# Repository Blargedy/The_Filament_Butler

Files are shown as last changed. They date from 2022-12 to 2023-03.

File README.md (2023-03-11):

# The Filament Butler
In short, this is a manually-operated drop-in replacement for the Prusa MMU2, for use in high(ish) temperature printing. 



I put my two Prusa Mk3s into enclosures in order to print ABS/ASA without warping. Unfortunately, the control boards of each MMU couldn't handle the elevated temperatures (~50C) and burned out. Instead of moving the electronics of the MMU2 out of the hot chamber, I decided to completely eliminate the automated swapping of filament.  I run the [Tefnut](https://github.com/Blargedy/Tefnut_Filament_Handling) system and wanted to maintain compatibility with it. The Filament Butler uses M10 PC6 pneumatic fittings to attach the 6mm OD tubing of Tefnut and proffers each filament to the operator for easy manual swapping, all without having to open the drybox lids.



# Instructions


1. Print all parts using the default orientation, without supports.

1. Insert M3 hex nuts in the following locations, using M3 screws to pull them into the pockets. 



1. insert M3 square nuts in the following locations, aligning their holes with the cylindrical screw holes.


1. Fasten the Pneumatic fitment bar to the main body with three M3x10 SHCS.


1. Attach the Frame Brackets with four M3x12 SHCS.


1. Cut five 41.5mm lengths of 4mm OD 2mm ID PTFE tubing, and place them in the Filament Stow Sections.
2. Secure the tubes with the Filament Stow Lid and four M3x22 SHCS.


1. Melt in two M3 heatserts into the Selector Body.


1. Press fit the collar insert into the Selector Collet.


1. Attach the Selector Collet to the Selector Body with two M3x10 SHCS.


1. Using a rubber mallet, insert the brass inserts into the tabbed slots on the Selector Body.


1. Slide the Selector Rails through the holes on the side of the Main Body, through the brass inserts, and into the holes on the far side of the Main Body.


1. Screw on the pneumatic fittings onto the Fitement Bar.


You are now done with the assembly of the Filament Butler itself. Next up is installing it and getting everything ready for printing:

3. Hook the unit onto the frame of the prusa, exactly like the MMU2s
4. Screw on the 4mm OD tubing pneumatic fitment to the collar on the Selector.
5. Push-fit the 6mm OD tubing to the pneumatic fitment bar fittings.
6. Load the filament through until the ends reach the far side of the Filament Stow section

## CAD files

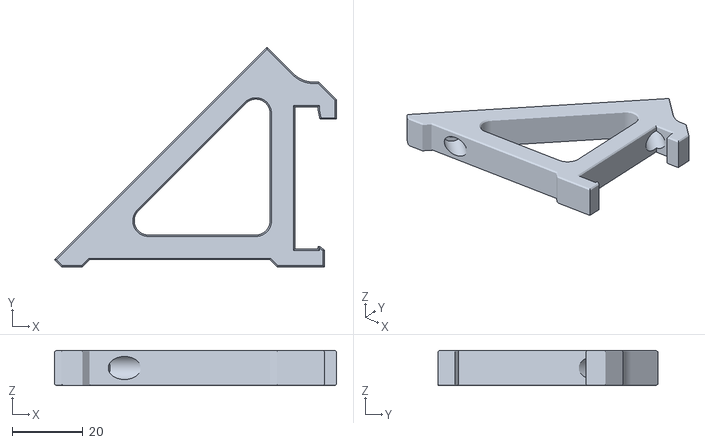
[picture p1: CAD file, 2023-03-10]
STLs/Prusa_MMU2_Frame_Bracket_x2.stl
79.8 x 62.1 x 10.0

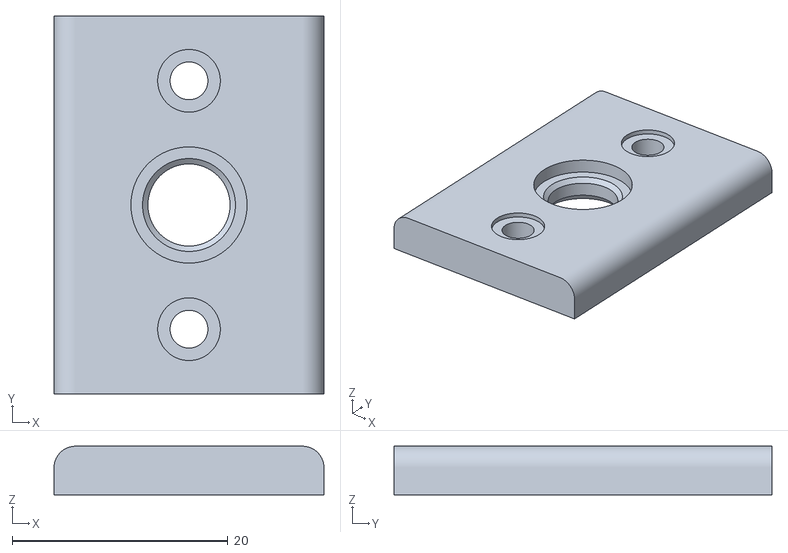
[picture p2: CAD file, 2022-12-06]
STLs/The_Filament_Butler_Selector_Collet.stl
25.0 x 35.0 x 4.50

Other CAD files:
CAD/The-Filament-Butler v13.f3d

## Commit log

2022-12-06 initial upload
    [The_Filament_Butler_Selector_Collet.stl]
2023-03-10 add missing file
    [Prusa_MMU2_Frame_Bracket_x2.stl]
2023-03-11 added f360 files
    [Prusa_MMU2_Frame_Bracket_x2.stl, The-Filament-Butler v13.f3d, The_Filament_Butler_Selector_Collet.stl]
